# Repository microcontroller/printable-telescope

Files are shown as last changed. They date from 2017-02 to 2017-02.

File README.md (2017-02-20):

# 3D printable-telescope

This is a simple 3D-printable Newtonian telescope requiring minimal parts.
We constructed ours using the following parts:

 * An old magnifying shaving mirror (note this is not parabolic)
 * A small [oval mirror](https://www.amazon.com/gp/product/B0018N5Q8E) from Amazon.
 * A piece of black posterboard cardstock rolled into a tube
 * Two curved erector set beams, with nuts and bolts
 * #8-32 threaded rod, with nuts and washers
 * [50mm concave lens](https://www.amazon.com/gp/product/B00BIKGMZ8) by Eisco

The top and bottom parts have both an inner and outer ring, and the cardboard
tube fits in the space between these two rings. All other parts use only the
outer ring.

As you can probably imagine, with an off-the-shelf shaving mirror, the optics
are less than ideal (actually it's terrible) but hopefully the same recipe will
work for whatever primary mirror and secondary mirror you are able to obtain.
In most telescopes, the primary mirror is the most sensitive component and the
most costly. You'll need a high-quality parabolic mirror if you want to
actually see anything more than a smudge through the telescope. Once you have
your mirrors, you'll just need to adjust a few parameters to get the prints for
your telescope.

Note that there's nothing in this design to hold the primary mirror against the
tube. It should be easy enough to print something to do this, but exactly what
you need will depend on the shape of your mirror housing. If you have a specific
need then by all means raise an issue and I'll see what I can come up with.

## Configuration and Printing

Here is a picture of the 3D model from [OpenSCAD](http://www.openscad.org):
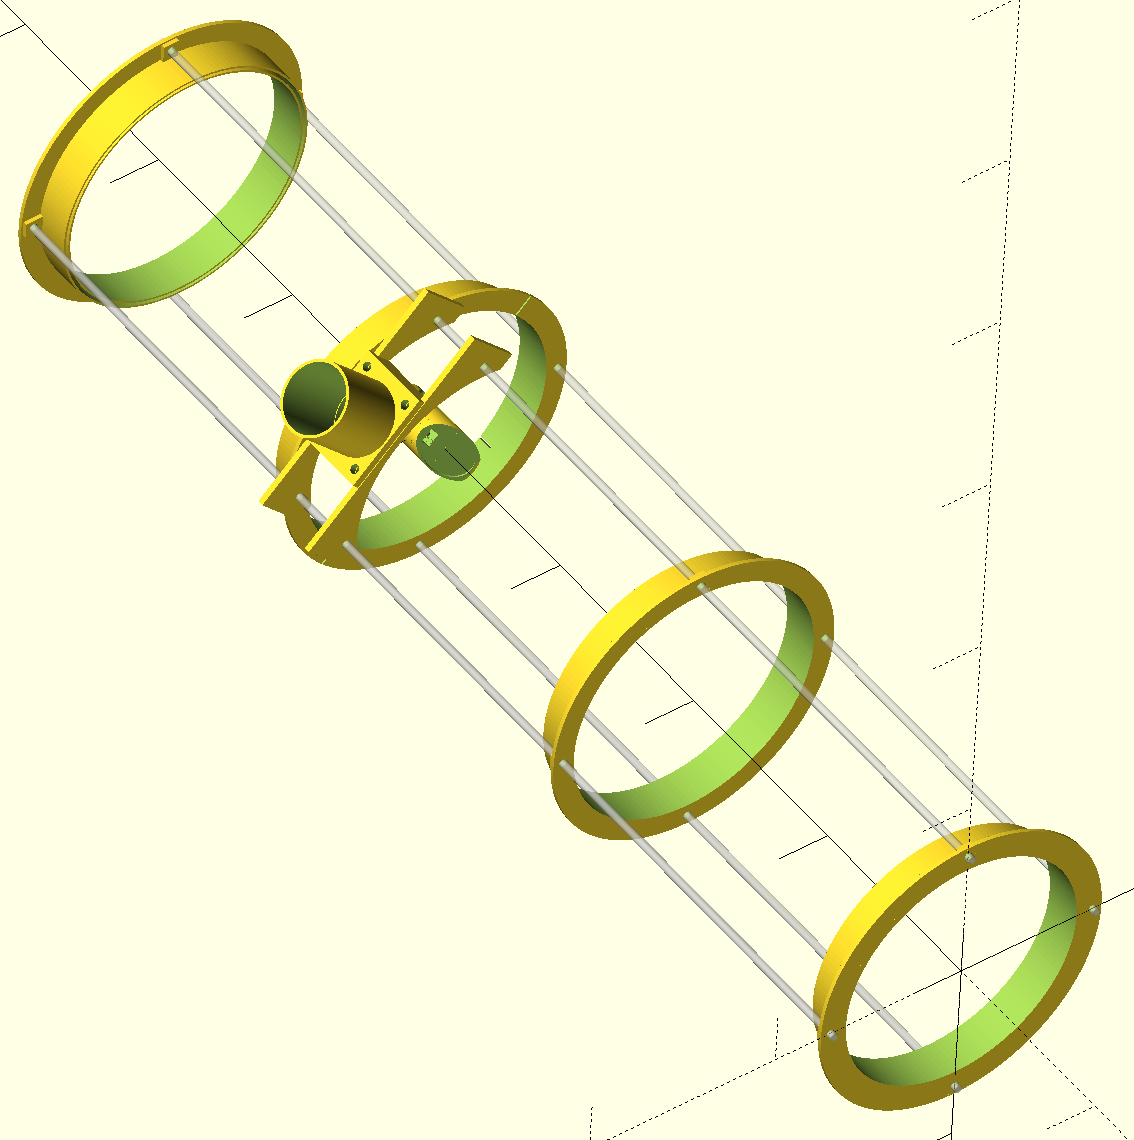
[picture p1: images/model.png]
3D model


Here is a picture of the almost-completely assembled telescope
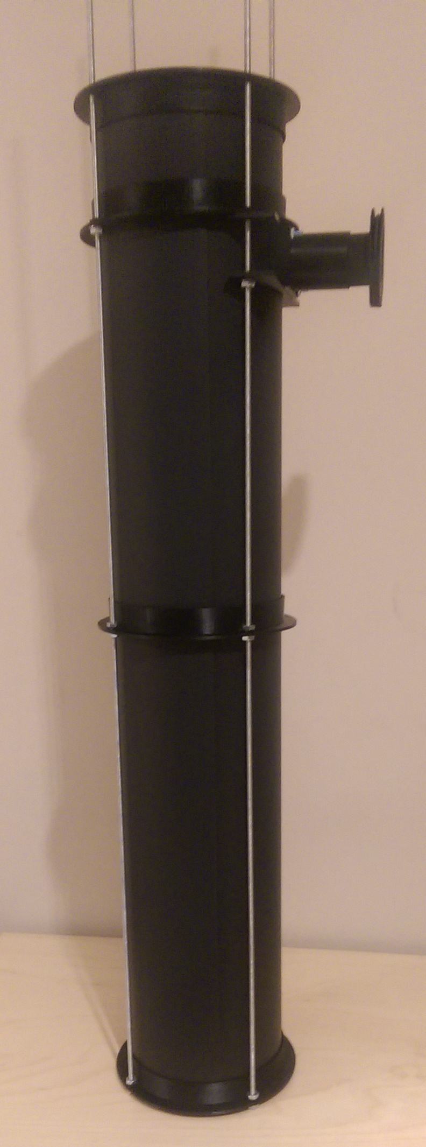
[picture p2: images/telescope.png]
Almost complete


The first step is of course measuring your objective mirror (`base_r1` in the
SCAD file). This determines the size of the tube pieces. Once it is set, you
can print out two of the `tube_base()` and one or more `tube_ring()` to hold
the cardboard cube in place.

You can also at this point print the `eyepiece_tube()` part to hold the
eyepiece assembly onto the threaded rods. The `eyepiece_tube_2()` part extends
the eyepiece tube, and is held on with erector-set nuts and bolts. The size
here is compatible with standard 1.25" eyepieces, and in case it helps I've
included an `lens_extender()` part that allows you to slide an eyepiece in
and out. There's no fancy rack-n-pinion system here - just friction holding it
all in place.

The `lens_tube()` part is a little tricky - in order to be printed in one piece,
it needs to be printed in the same orientation it's used in. However, this needs
support when printing. Unless you have a high-end printer that can print
dissolvable support material, you don't want to enable support as the result
will most likely be a filled-in inner tube that you can't clean up. Instead, I
came up with a minimalist support structure that should be easy to remove but
will provide sufficient support. So use `lens_tube_printable()` to generate
that.

You'll also need to measure your secondary mirror. I've assumed that it's oval
in shape, and the radii are `secondary_r1` and `secondary_r2` in the SCAD file.
The secondary mirror is glued to a mirror mount that holds it steady at 45
degrees. Inserted into the mirror mount are two erector-set / meccano "strip"
beams at 90 degrees from each other. Once you've adjusted the mirror radii
parameters, and ensured that the support beams line up with the notches in
`tube_ring_cut()` you're ready to print that part and the `mirror_mount()` part.
Test that it works and lines up with having the eyepiece assembly below it.
This is what ours looks like:

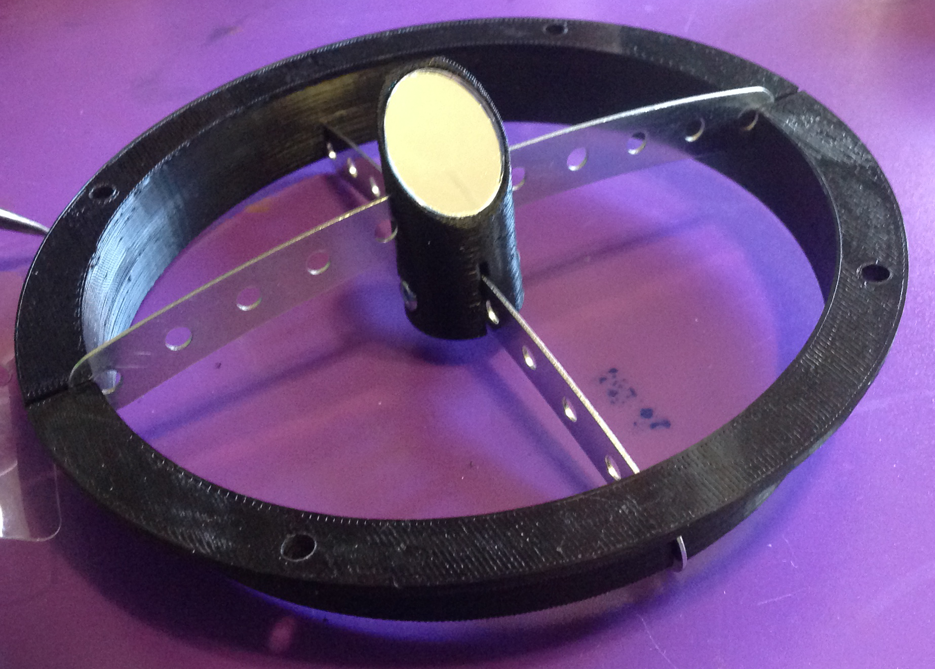
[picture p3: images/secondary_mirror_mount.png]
Secondary Mirror


If you need to adjust the height / width of the notches, or the height of the
secondary mirror mount, go ahead and do whatever works best for you, or raise
an issue and I'll see what I can do. It's probably best to keep the theme of
having one over and one under the supporting ring, and just adjust the bolt/nut
holes in the secondary mirror mount to fit whatever hardware you have available.

When you're done with printing, you should have the following parts (plus of
course the black posterboard):

Parts

## Assembly

First we start threading nuts onto the threaded rod. Unless you increase
`base_r5` you'll find that you can't fit a washer on the top side of the rings,
so your parts go on as:

 * top nut
 * ring / other part
 * washer
 * bottom nut

Obviously for the top ring this order is reversed. The best order for threading
is this:

 1. top nuts for ring
 2. ring
 3. washers and bottom nuts for ring
 4. top nuts for base dual-ring
 5. base dual-ring
 6. washers and bottom nuts for base
 7. 2x washers bottom nuts for eyepiece assembly
 8. eyepiece assembly
 9. 2x washers and bottom nuts for notched mirror mount ring
 10. notched ring with mirror mount
 11. top nuts for notched ring
 12. bottom nuts for top dual-ring

At this point, pause and use your secondary mirror to determine the best place
(vertically) for the eyepiece assembly. You should be able to look through the
eyepiece tube, see the secondary mirror in center view, and through it see all
of the inner base ring. We found that the notched ring fit immediately above
the eyepiece assembly, and we rested it on top of that on two of the threaded
rods. Verify that the vertical alignment is correct for your configuration, and
adjust if necessary.

Now remove the two erector-set strip beams (or whatever you're substituting)
that hold the secondary mirror mount in place. Insert the black posterboard,
feeding it down and into the gap between the two rings. Put on the top dual-ring
piece, but you don't need to tighten any nuts at this stage as friction will
hold it in place. You'll need to cut slots into the posterboard to accommodate
your mirror mount, and make a circular hole to allow the eyepiece to actually
see anything. Make sure that everything is level before you start, mark the
position of the holes, and then move the notched ring up and out of the way so
you can start cutting.

Once you've made the cuts, now comes the tricky part - reinsert the mirror mount
supports so that they're held in place by the notched ring and they're locked in
place with the necessary bolts. We first put the lower support beam (closest to
the secondary mirror) and bolted that in place, then glued the secondary
mirror on, and inserted this partially assembled piece into the notches in the
notched ring through the slots in the poasterboard. Then we inserted the second
support beam, getting it in place in the notched ring before bolting it into the
secondary mirror mount.

Now, finally, you can tighten all the nuts to hold everything securely in place.
Hold the primary mirror in place, look through the eyepiece hole (without any
lens) to make sure you can see something, and then try it with a magnifying
eyepiece.

Give yourself a high five - you just made a telescope!

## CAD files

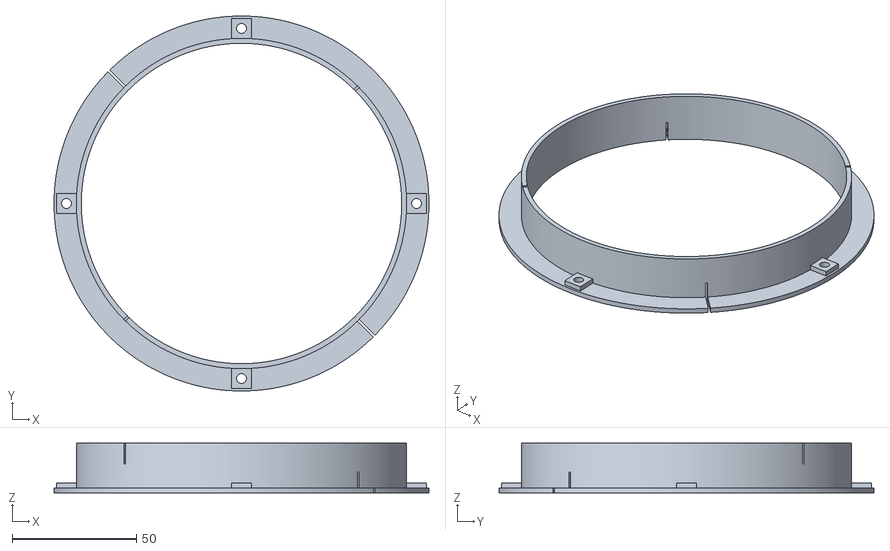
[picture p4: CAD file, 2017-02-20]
STL/2016-12-mirror_tube_ring_cut.stl
151.0 x 151.0 x 20.0

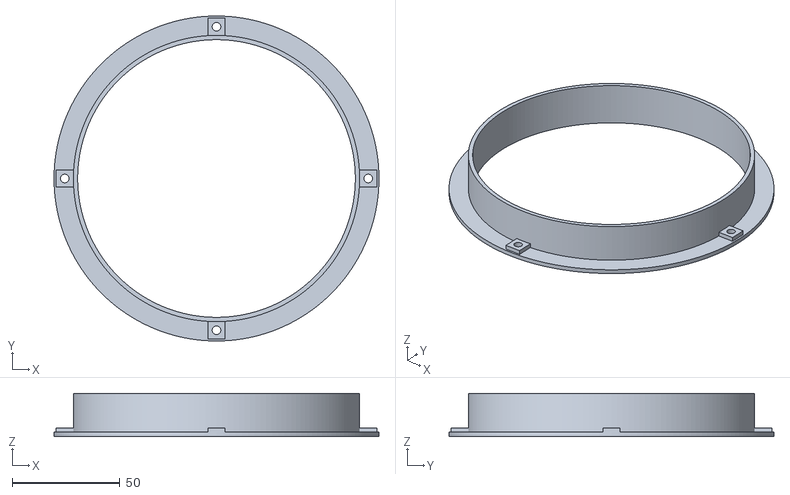
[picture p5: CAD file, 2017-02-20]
STL/2016-12-mirror_tube_ring.stl
151.0 x 151.0 x 20.0

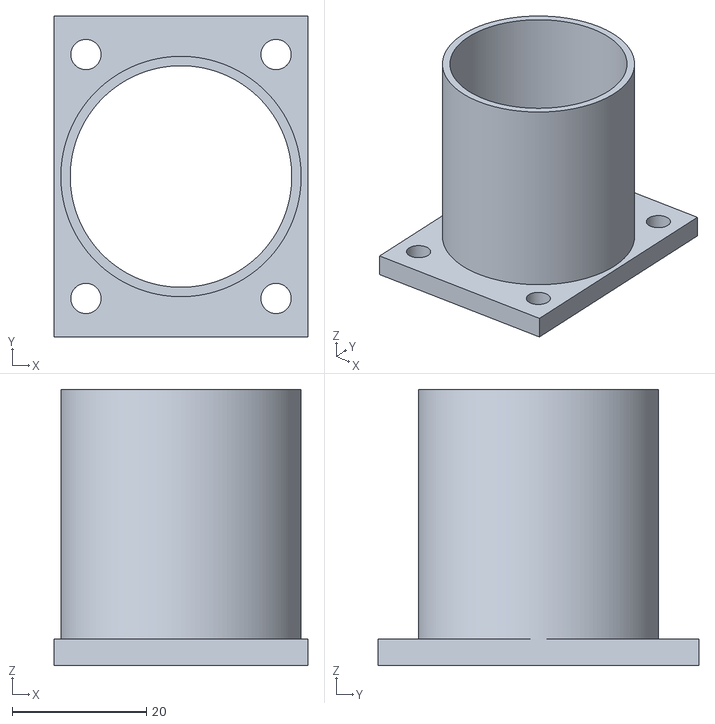
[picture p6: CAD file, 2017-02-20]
STL/2016-12-mirror_eyepiece_mount_tube.stl
37.8 x 47.8 x 41.1

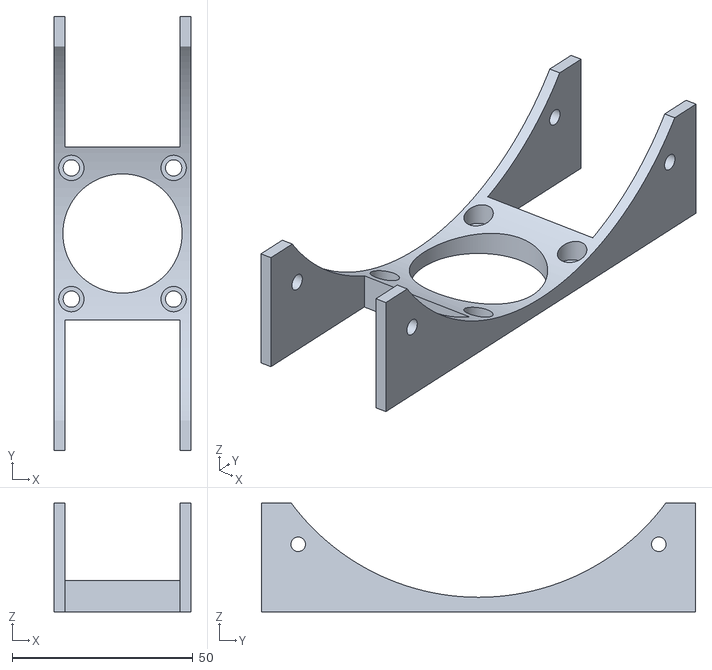
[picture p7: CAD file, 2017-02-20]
STL/2016-12-mirror_eyepiece_mount.stl
37.8 x 120.0 x 30.0

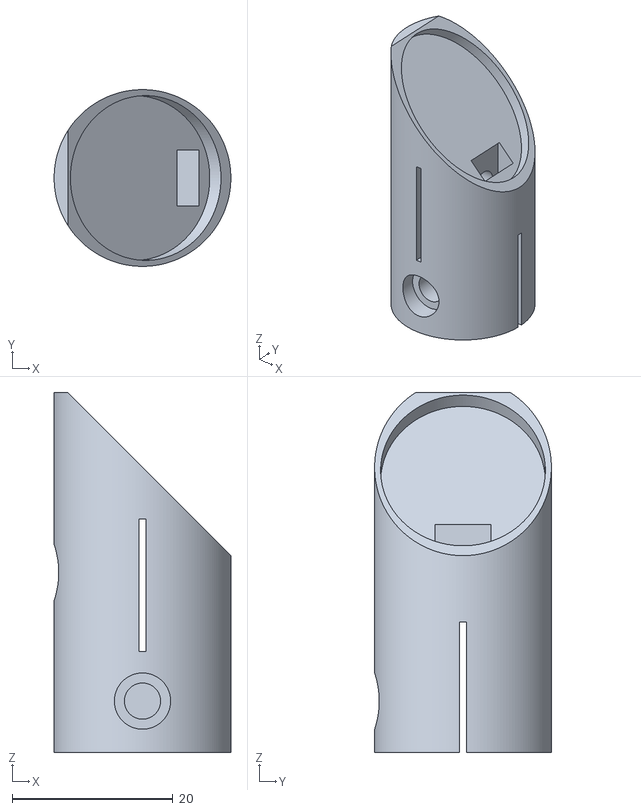
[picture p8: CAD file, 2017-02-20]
STL/2016-12-mirror_mount.stl
22.0 x 22.0 x 44.8

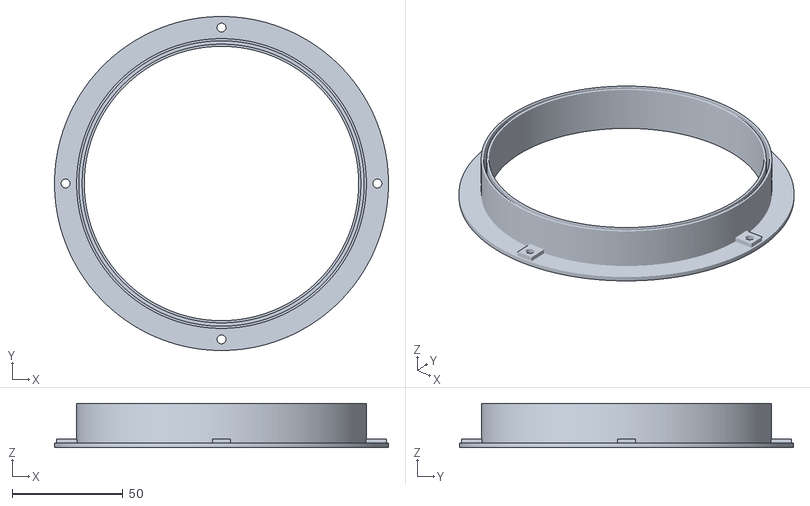
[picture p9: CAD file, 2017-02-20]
STL/2016-12-mirror_tube_base.stl
151.0 x 151.0 x 20.0

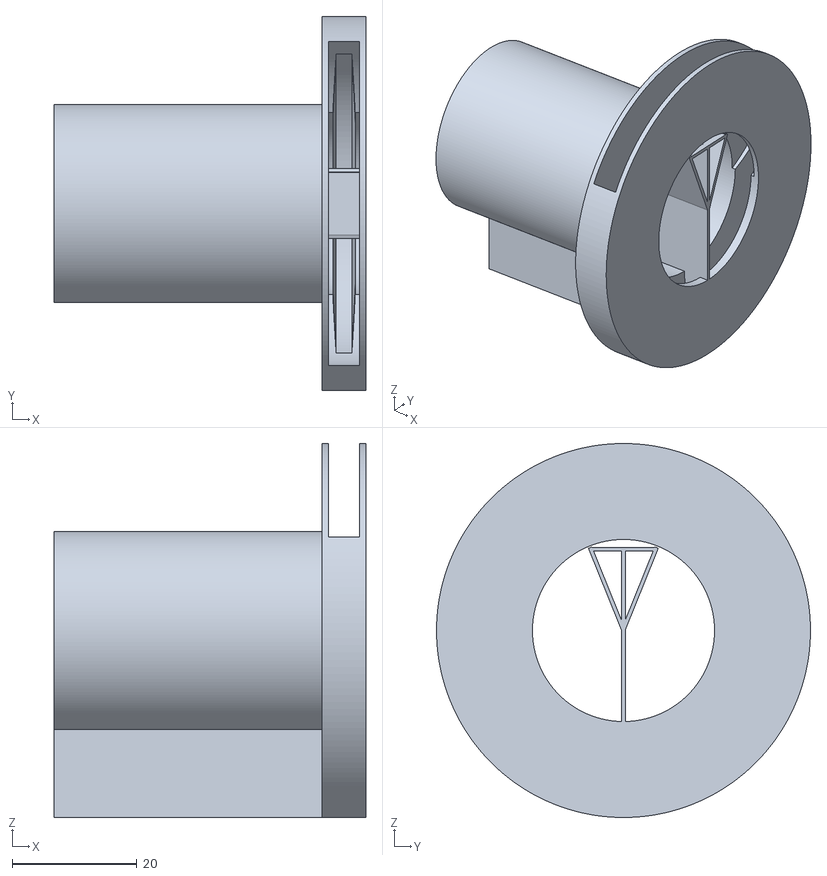
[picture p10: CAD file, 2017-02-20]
STL/2016-12-mirror_drawtube.stl
50.0 x 60.0 x 60.0

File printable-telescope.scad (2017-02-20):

$fn = 160;
beam_x = 82.6;
beam_r = 6.4;
beam_d = beam_r * 2;
inch = 25.4;

rod_r = 2;

base_z = 20;
base_r1 = 62;
base_r2 = base_r1 + 1;
base_r3 = base_r1 + 2.5;
base_r4 = base_r1 + 3.5;
base_r5 = base_r1 + 13.5;

secondary_r1 = 13.25;
secondary_r2 = 10.25;

module erector_beam() {
    translate([0, 0, -0.45])
        hull() {
            cylinder(r = beam_r + 0.25, h = 0.9);
            translate([beam_x, 0, 0])
                cylinder(r = beam_r + 0.25, h = 0.9);
        }
}
module mirror() {
    scale([1, secondary_r2 / secondary_r1, 1])
        cylinder(r = secondary_r1, h = 2);
}


module mount_hardware() {
    translate([-1, 0, beam_d * 2 + beam_r * 1.5 - 1.5])
        rotate([0, 45, 0]) {
            mirror();
            translate([0, 0, 1.98])
                scale([1.5, 1.5, 10])
                    mirror();
        }
    translate([0, 0, beam_r * 1.5])
        rotate([90, 0, 0])
            translate([-beam_x / 2, 0, 0])
                erector_beam();
    rotate([90, 0, 0])
        translate([-beam_x / 2, 0, 0])
            erector_beam();
    translate([0, 0, beam_d + beam_r * 1.5])
        rotate([90, 0, 90])
            translate([-beam_x / 2, 0, 0])
                erector_beam();
    translate([0, 0, beam_d + beam_r])
        rotate([90, 0, 90])
            translate([-beam_x / 2, 0, 0])
                erector_beam();
    translate([-11.02, 0, beam_d + beam_r * 1.5])
        rotate([0, 90, 0]) {
            cylinder(r = 2.25, h = 18);
            cylinder(r = 3.5, h = 3);
        }
    translate([4, -3.5, beam_d + beam_r * 1.5 -4]) {
        cube([3, 7, 10]);
        //#cube([3, 7, 7.5]);
    }
    translate([0, -11.02, beam_r])
        rotate([0, 90, 90]) {
            cylinder(r = 2.25, h = 18);
            cylinder(r = 3.5, h = 3);
        }
    translate([-3.5, 4, -0.02]) {
        cube([7, 3, 11]);
    }
}

module mirror_mount() {
    difference() {
        cylinder(r = 11, h = beam_d * 3.5);
        mount_hardware();
    }
}


module nuts() {
    for (r = [0 : 90 : 270]) {
        rotate([0, 0, r]) {
            translate([1-base_r5, -4, 0]) {
                cube([base_r5 - base_r4 - .5, 8, 4]);
            }
        }
    }
}

module rods(h = 10) {
    for (r = [0 : 90 : 270]) {
        rotate([0, 0, r]) {
            translate([-(base_r5 + base_r4) / 2, 0, -0.02]) {
                cylinder(r = rod_r, h = h + 0.04);
            }
        }
    }
}

module tube_ring() {
    difference() {
        union() {
            cylinder(r = base_r5, h = 2);
            cylinder(r = base_r4+1, h = base_z);
            nuts();
        }
        translate([0, 0, -.1])
            cylinder(r = base_r3, h = base_z + 0.2);
        rods();
    }
}

module tube_ring_cut() {
    difference() {
        tube_ring();
        
        translate([0, 0, 30])
            rotate([90, 10, 45])
                erector_beam();
        translate([0, 0, 30])
            rotate([90, 10, 180+45])
                erector_beam();
        translate([0, 0, -10])
            rotate([-90, -10, -45])
                erector_beam();
        translate([0, 0, -10])
            rotate([-90, -10, 180-45])
                erector_beam();
    }
}

module tube_base() {
    difference() {
        union() {
            cylinder(r = base_r5, h = 2);
            cylinder(r = base_r2, h = base_z);
            nuts();
        }
        translate([0, 0, -.1])
            cylinder(r = base_r1, h = base_z + 0.2);
        rods();
    }
    difference() {
        cylinder(r = base_r4, h = base_z);
        translate([0, 0, 2])
            cylinder(r = base_r3, h = base_z);
        translate([0, 0, -.1])
            cylinder(r = base_r1, h = base_z + 0.2);
    }
}

module lens() {
    cylinder(r1=1,r2=25.5, h=1.25);
    translate([0, 0, 1.23])
        cylinder(r=25.5, h=2.54);
    translate([0, 0, 3.75])
        cylinder(r1=25.5, r2=1, h=1.25);
}

module lens_tube(support = true) {
    difference() {
        union() {
            cylinder(r=30, h=7);
            cylinder(r = 1.25 * inch / 2 - .6, h = 50);
            /*
            translate([-30, -.3, 0])
                cube([30 - 1.25 * inch / 2, .6, 50]);
            translate([-30, - 1.25 * inch / 2, 0])
                cube([30, .6, 50]);
            translate([-30, 1.25 * inch / 2 - .6, 0])
                cube([30, .6, 50]);
            translate([-30, - 1.25 * inch / 4, 0])
                cube([30, .5, 50]);
            translate([-30, 1.25 * inch / 4 - .6, 0])
                cube([30, .6, 50]);
            */
        }
        translate([0, 0, 1])
            lens();
        translate([16, 0, 1])
        scale([.75, 1, 1])
            cylinder(r = 26, h=5);
        translate([0, 0, -.02])
            cylinder(r = 1.15 * inch / 2, h = 50.04);
    }
    if(support) {
    translate([-30, -.3, 0])
        cube([30 + 1.05 * inch / 2, .6, 50]);
    translate([sin(22)*.6, -.3, 0])
    rotate([0, 0, 22])
        cube([1.12 * inch / 2, .6, 50]);
    translate([0, -.3, 0])
    rotate([0, 0, -22])
        cube([1.12 * inch / 2, .6, 50]);
    translate([cos(22)*1.08 * inch / 2, -.25-sin(22)*1.05 * inch / 2, 0])
        cube([.6, sin(22)*1.05 * inch+.5, 50]);
    }
}

module lens_extender() {
    difference() {
        union() {
            cylinder(r = 1.25 * inch / 2 - .6, h = 100);
            cylinder(r = 2 + 1.25 * inch / 2, h = 30);
        }
        translate([0, 0, -.1])
            cylinder(r = +1.25 * inch / 2, h = 28);
        cylinder(r = 1.15 * inch / 2, h = 100.1);
    }
}

module lens_tube_printable() {
    rotate([0, -90, 0])
        lens_tube(support = true);
}

module eyepiece_holes() {
    rotate([0, -90, 0]) {
        cylinder(r = +1.25 * inch / 2, h = 5 * inch);
        for(r = [0 : 90 : 90]) {
            translate([0, -4, 0]) {
                rotate([0, 0, r + 45]) {
                    translate([-20, 0, 60]) {
                        cylinder(r = 2.25, h = 18);
                        cylinder(r = 3.5, h = 6);
                    }
                }
            }
        }
        for(r = [180 : 90 : 270]) {
            translate([0, 4, 0]) {
                rotate([0, 0, r + 45]) {
                    translate([-20, 0, 60]) {
                        cylinder(r = 2.25, h = 18);
                        cylinder(r = 3.5, h = 6);
                    }
                }
            }
        }
    }
}

module eyepiece_tube_2() {
    difference() {
        union() {
            rotate([0, 0, 0]) {
                translate([-base_r4 - 7.5, -1.25 * inch / 2 - 8, -3 - 1.25 * inch / 2])
                    cube([4, 1.25 * inch + 16, 1.25 * inch + 6]);
            }
            rotate([0, -90, 0]) {
                translate([0, 0, 72]){
                    cylinder(r = 2 + 1.25 * inch / 2, h = inch * 1.5);
            }}
        }
        eyepiece_holes();
    }
}

module eyepiece_tube() {
    difference() {
        translate([0, 0, -3 - 1.25 * inch / 2]) {
            union() {
                translate([-base_r4 - 3, -60, 0])
                    cube([30, 120, 3]);
                translate([-base_r4 - 3, -60, 1.25 * inch + 3])
                    cube([30, 120, 3]);
                translate([-base_r4 - 3, -1.25 * inch / 2 - 8, 0])
                    cube([30, 1.25 * inch + 16, 1.25 * inch + 6]);
                cylinder(r = 50, h = 10);
            }
        }
        translate([0, 0, -3.02 - 1.25 * inch / 2])
            cylinder(r = base_r3, h = 2 * inch + 0.04);
        translate([0, 0, -3 - 1.25 * inch / 2]) {
            rotate([0, 0, 45]) {
                rods(2 * inch);
            }
        }
        eyepiece_holes();
    }
    
}

module display_model() {
    tube_base();
    translate([0, 0, 200])
        tube_ring();
    translate([0, 0, 400])
        tube_ring_cut();
    translate([0, 0, 419])
        rotate([0, 180, 45])
            mirror_mount();
    translate([0, 0, 381])
        rotate([0, 180, 180+45])
            eyepiece_tube();
    translate([0, 0, 381])
        rotate([0, 0, 45])
    eyepiece_tube_2();
    translate([0, 0, 600])
        rotate([0, 180, 0])
            tube_base();
    translate([0, 0, -3]) {
        %rods(h = 606);
    }
    translate([0, 0, 381])
        rotate([-90, 0, -45]) {
            translate([0, 0, -base_r5-130])
                lens_tube(support = false);
            translate([0, 0, -base_r5-100])
                lens_extender();
        }
}


display_model();

//tube_ring_cut();
//rotate([0, -90, 0])
//    eyepiece_tube();
//rotate([0, 90, 0])
//    eyepiece_tube_2();

//mirror_mount();

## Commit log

2017-02-20 This dropped off my radar for a while, but it's ready to go now.
    [2016-12-mirror_drawtube.stl, 2016-12-mirror_eyepiece_mount.stl, 2016-12-mirror_eyepiece_mount_tube.stl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]
2017-02-20 Changed file permissions
    [2016-12-mirror_drawtube.stl, 2016-12-mirror_eyepiece_mount.stl, 2016-12-mirror_eyepiece_mount_tube.stl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]
